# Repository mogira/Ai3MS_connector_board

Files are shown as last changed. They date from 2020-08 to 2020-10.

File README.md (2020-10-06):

# Anycubic i3 Mega S Connector Board
## Overview
This is the project to create the connector board for ["MONOBLOCK" ANYUCBIC I3 MEGA-S Direct Extruder MOD add BLTouch by Toshi_Yamamoto](https://www.thingiverse.com/thing:4035830).  
The board accepts BLTouch, Extruder Motor and the extension cords to these from motherboard additinally.

### Remarks
**If you need switch, capacitors and resistors of the stock board, you can not use this board because I removed them.**

<br />

## [>> Build Guide](docs/build_guide.md)

<br />

## [>> CADLAB.io](https://cadlab.io/node/23246/)

<br />

## [>> Circuit Board Gallery](docs/circuit_board_gallery.md)

<br />

## Gallery
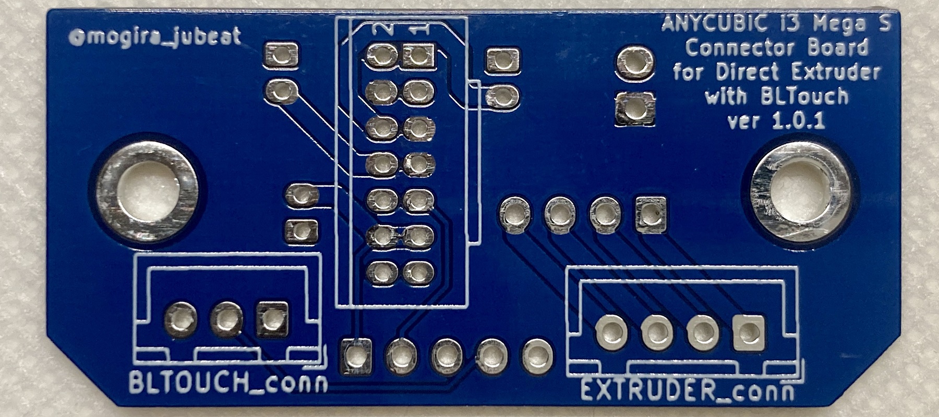
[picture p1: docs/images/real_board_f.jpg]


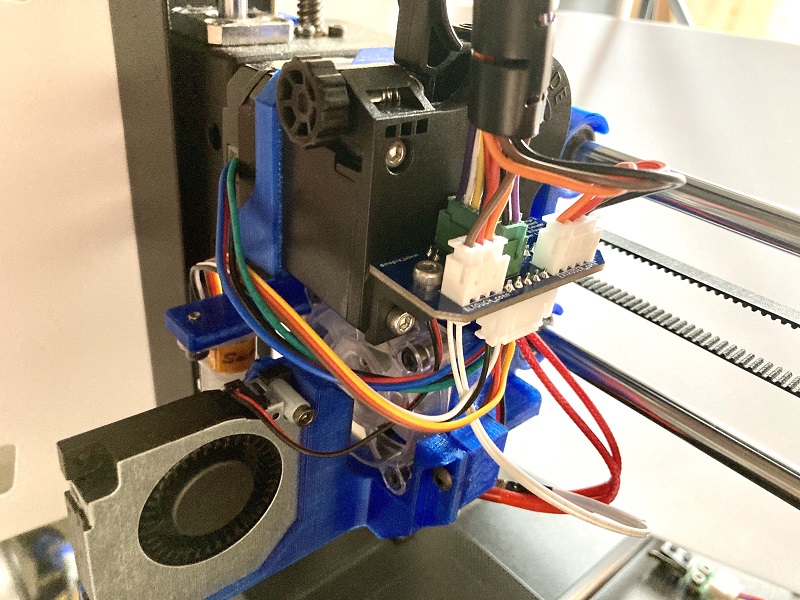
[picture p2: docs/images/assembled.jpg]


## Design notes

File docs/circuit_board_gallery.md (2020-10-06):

# Cuircuit Board Gallery

| | Front | Back |
|-|---|---|
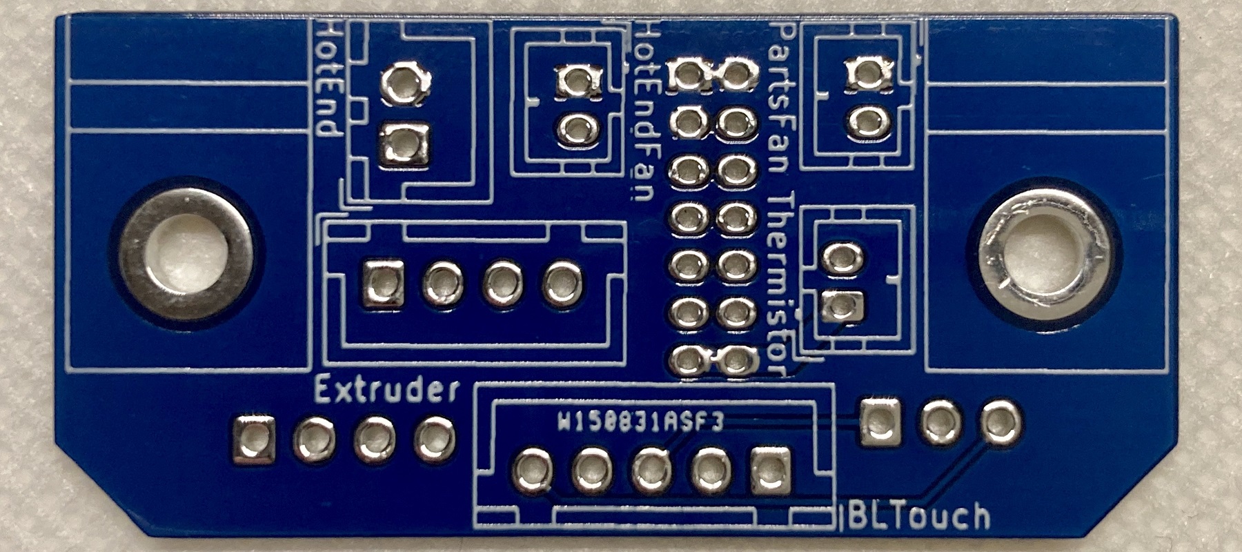
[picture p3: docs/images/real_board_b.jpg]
| Real Board |  |  |
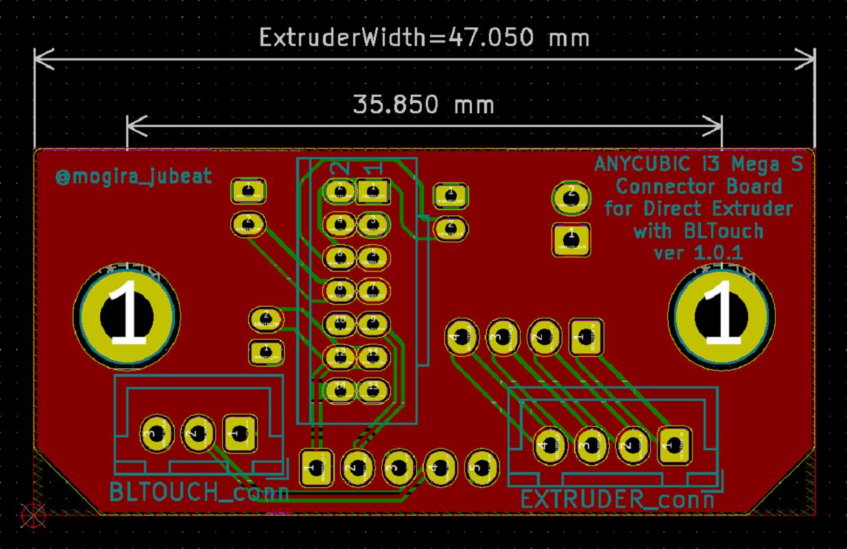
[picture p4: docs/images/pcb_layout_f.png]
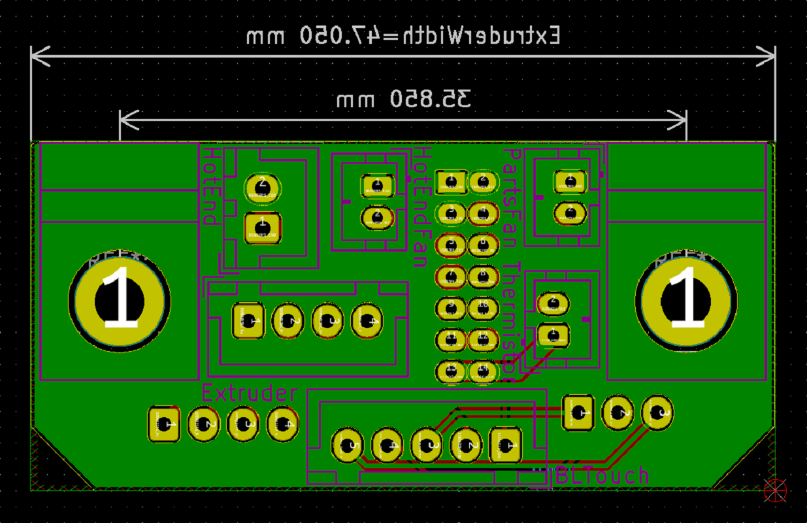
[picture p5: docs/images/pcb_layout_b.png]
| Layout |  |  |

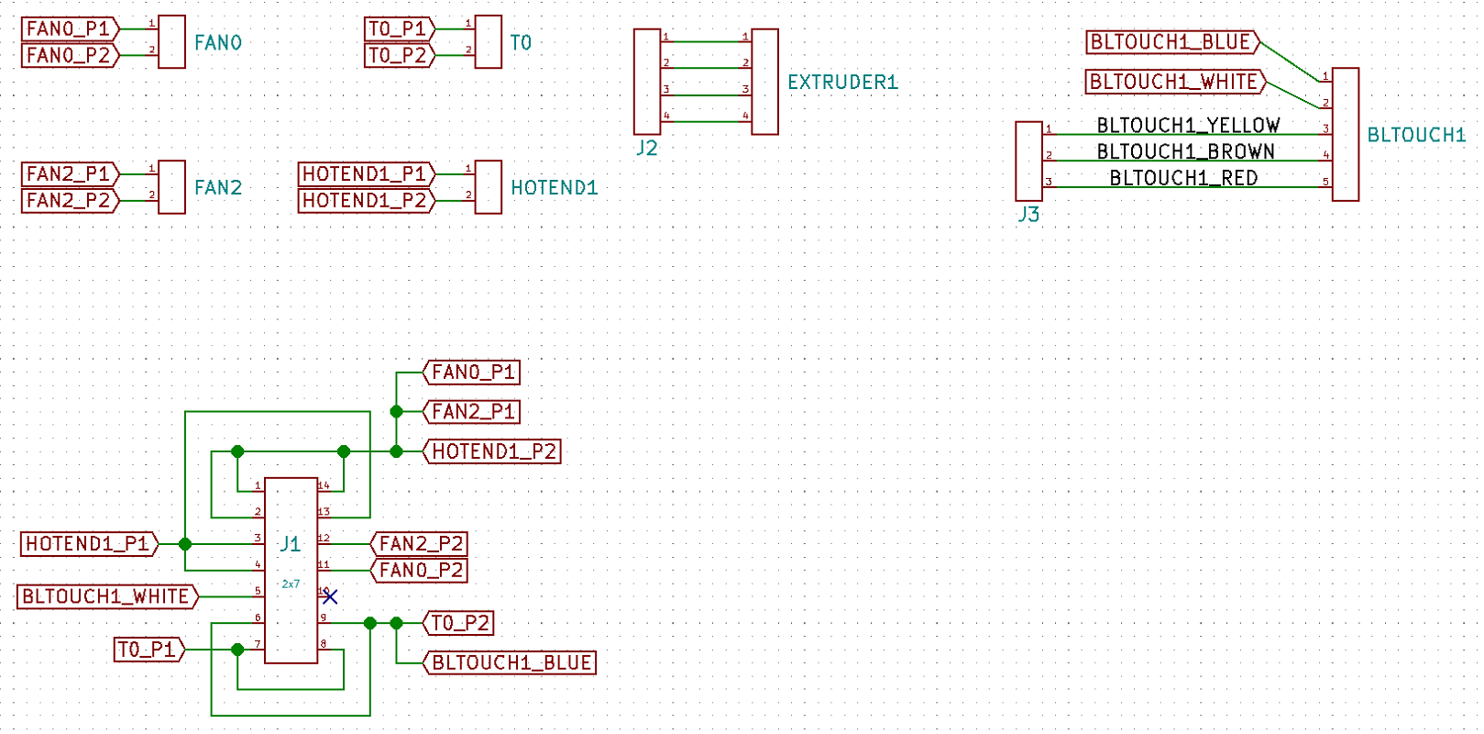
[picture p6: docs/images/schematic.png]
| Schematic |  |
|-|-|

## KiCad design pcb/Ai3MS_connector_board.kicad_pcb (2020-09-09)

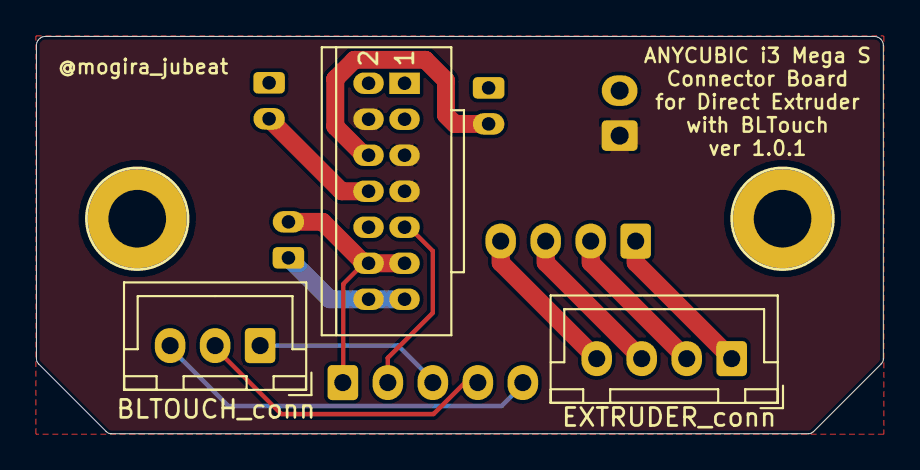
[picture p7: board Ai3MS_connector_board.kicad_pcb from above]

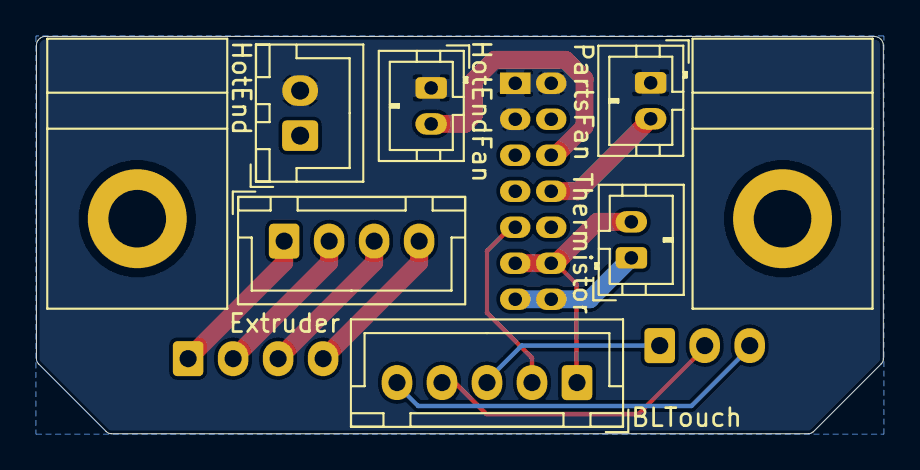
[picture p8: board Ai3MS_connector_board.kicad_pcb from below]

Board: 2 copper layers, 47.0 x 22.1 mm, 9 parts (6 on the bottom side), 14 nets.

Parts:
BLTOUCH_conn: 1x3_rev; JST_XH_B3B-XH-A_1x03_P2.50mm_Vertical
BLTouch: 1x5; JST_XH_B5B-XH-A_1x05_P2.50mm_Vertical
EXTRUDER_conn: 1x4_rev; JST_XH_B4B-XH-A_1x04_P2.50mm_Vertical
Extruder: 1x4; JST_XH_B4B-XH-A_1x04_P2.50mm_Vertical
HotEnd: 1x2; JST_XH_B2B-XH-A_1x02_P2.50mm_Vertical
HotEndFan: 1x2; JST_PH_B2B-PH-K_1x02_P2.00mm_Vertical
J1: 2x7; 2x7_2mm-pitch_Lock_GreenConnector
PartsFan: 1x2; JST_PH_B2B-PH-K_1x02_P2.00mm_Vertical
Thermistor: 1x2; JST_PH_B2B-PH-K_1x02_P2.00mm_Vertical

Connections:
/BLTOUCH1_SERVO_5V: BLTOUCH_conn.3, BLTouch.5
/BLTOUCH1_SERVO_CONTROL: BLTOUCH_conn.1, BLTouch.3
/BLTOUCH1_SERVO_GND: BLTOUCH_conn.2, BLTouch.4
/EXTRUDER1_A+: EXTRUDER_conn.1, Extruder.1
/EXTRUDER1_A-: EXTRUDER_conn.2, Extruder.2
/EXTRUDER1_B+: EXTRUDER_conn.3, Extruder.3
/EXTRUDER1_B-: EXTRUDER_conn.4, Extruder.4
BLTOUCH1_GND: BLTouch.1, J1.11, J1.12, Thermistor.2
BLTOUCH1_ZMIN: BLTouch.2, J1.9
HEATER1_12V: HotEnd.2, HotEndFan.1, J1.1, J1.2, J1.3, PartsFan.1
HEATER1_GND: HotEnd.1, J1.4, J1.5, J1.7
HOTENDFAN1_GND: HotEndFan.2, J1.6
PARTFAN1_GND: J1.8, PartsFan.2
THERMISTOR1_DATA: J1.13, J1.14, Thermistor.1

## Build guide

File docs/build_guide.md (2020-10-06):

# Build Guide
## Parts List
| Name | Quantity | Remark |
|---|:---:|---|
| MAC8 AXA-15-M3-3.2 | 2 | (can use but not recommend) or AXA-15-M3 |
| (2x7 2mm Pitch) Green Connector | 1 | transplant from the stock board |
| JST **PH** Female Connector 1x2 | 3 | |
| JST XH Female Connector 1x2 | 1 | |
| JST XH Female Connector 1x2 | 1 | |
| JST XH Female Connector 1x3 | 1 | |
| JST XH Female Connector 1x4 | 2 | |
| JST XH Female Connector 1x5 | 1 | |
| JST XH Male Connector 1x3 | 1 | |
| JST XH Male Connector 1x4 | 2 | |
| JST XH Male Connector 1x5 | 1 | |
| JST XH Connector Contact | 16 | |
| Dupont/QI/2550 Connector 1x1 | 3 | |
| Dupont/QI/2550 Connector Contact| 3 | |
| M3 Screw 50mm | 1 | |
| M3 Screw 30mm | 1 | |
| M3 Screw 6mm | 2 | |

And you need a crimp tool. I recommend "ENGINEER PA-09" to crimp XH and PH connectors.

<br />

## Notes
* Silks are changed from the stock board as below:
    * T0 -> Thermistor
    * FAN0 -> PartsFan
    * FAN2 -> HotEndFan

<br />

## Procedures
### 1. Remove the parts from the stock board
You must remove the Green Connector to transplant to the new board.  
About the other connectors, do as you like.  
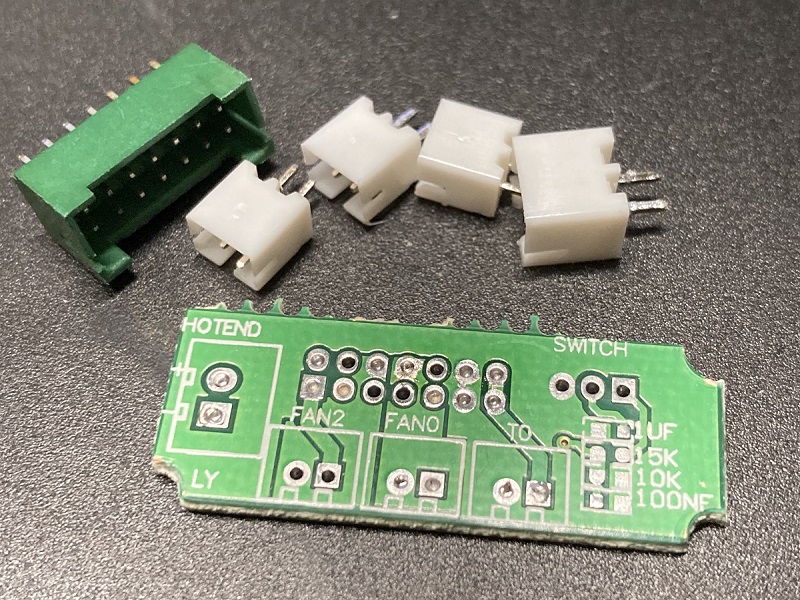
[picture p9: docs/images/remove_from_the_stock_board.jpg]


<br />

### 2. Expand the holes with drill
#### **AXA-15-M3 (recommend)**
If you substitute AXA-15-M3 for AXA-15-M3-3.2, it is better to expand the screw hole on the extruder side of it to 3.2mm (M3 Clearance hole size).  
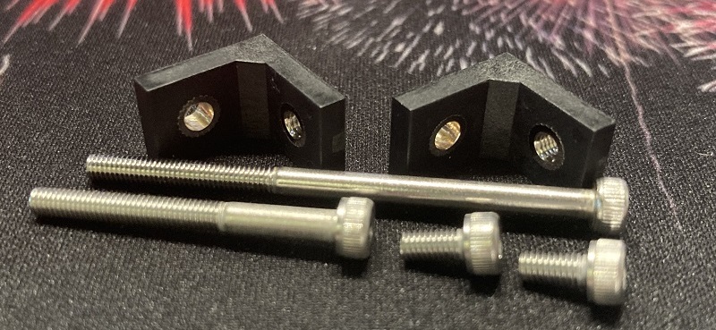
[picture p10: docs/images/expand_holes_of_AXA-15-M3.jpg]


<br />

### 3. Solder the parts to the board
It is easier to implement the GreenConnector firstly.  
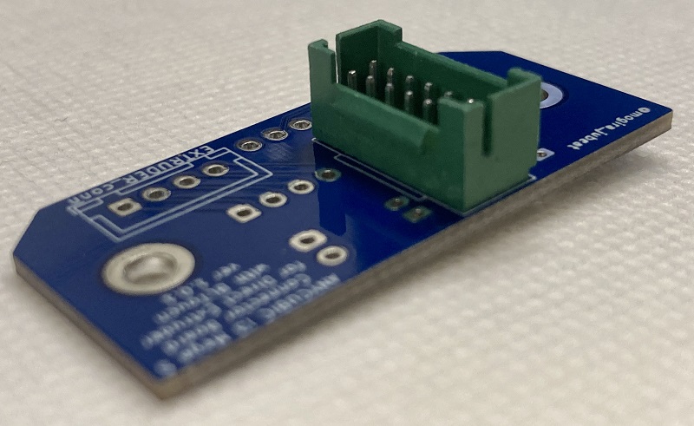
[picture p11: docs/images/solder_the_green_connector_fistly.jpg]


<br />

### 4. Crimp the connectors
You should crimp the following connectors:
* BLTOUCH_conn (1x3 XH)  
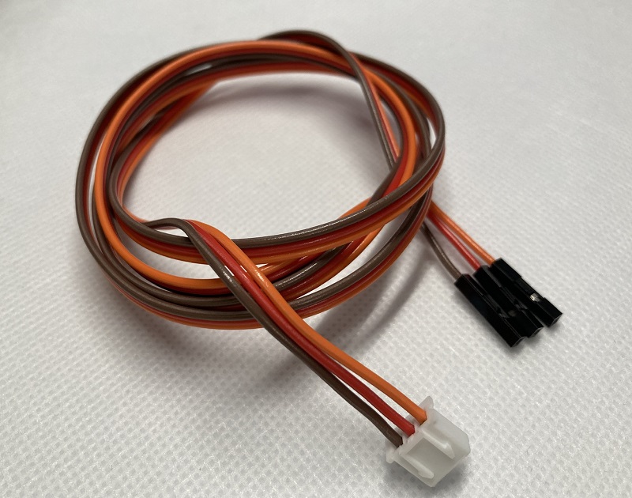
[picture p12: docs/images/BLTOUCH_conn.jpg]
  
* EXTRUDER_conn (1x4 XH)  
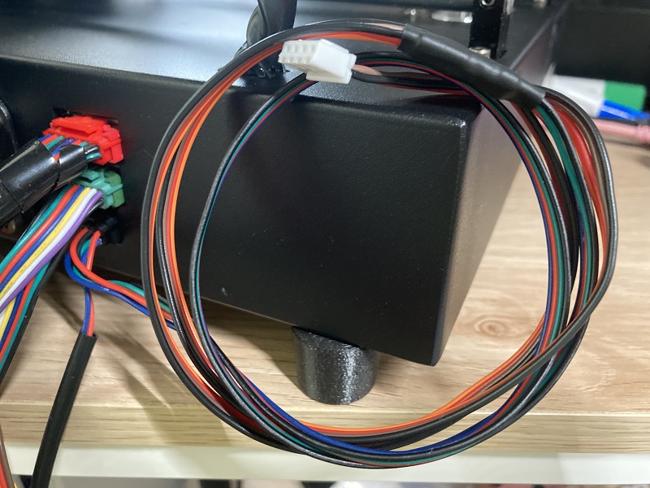
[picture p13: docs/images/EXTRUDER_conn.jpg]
    
  \* You should extend the Extruder connector cable to the print head.
* BLTouch (1x5 XH)  
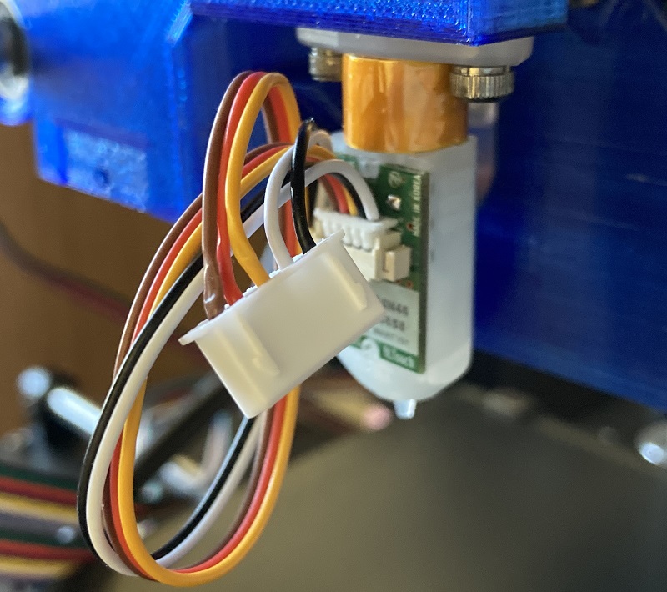
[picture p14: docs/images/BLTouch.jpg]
  
* Extruder (1x4 XH)  
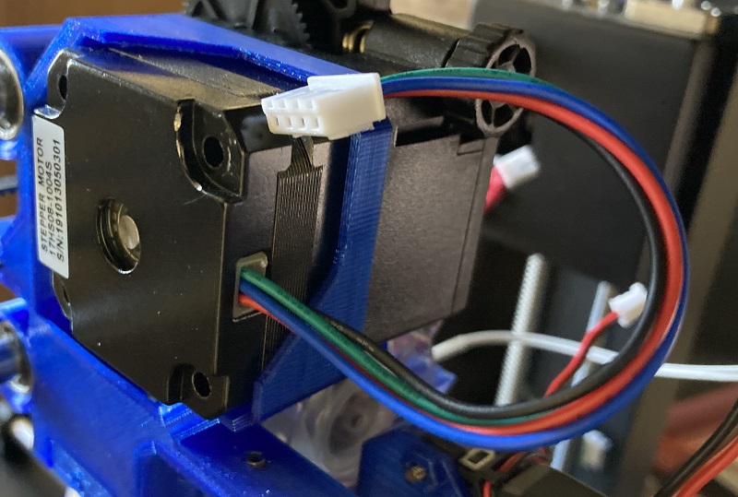
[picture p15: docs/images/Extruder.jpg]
  

<br />

### 5. Assemble
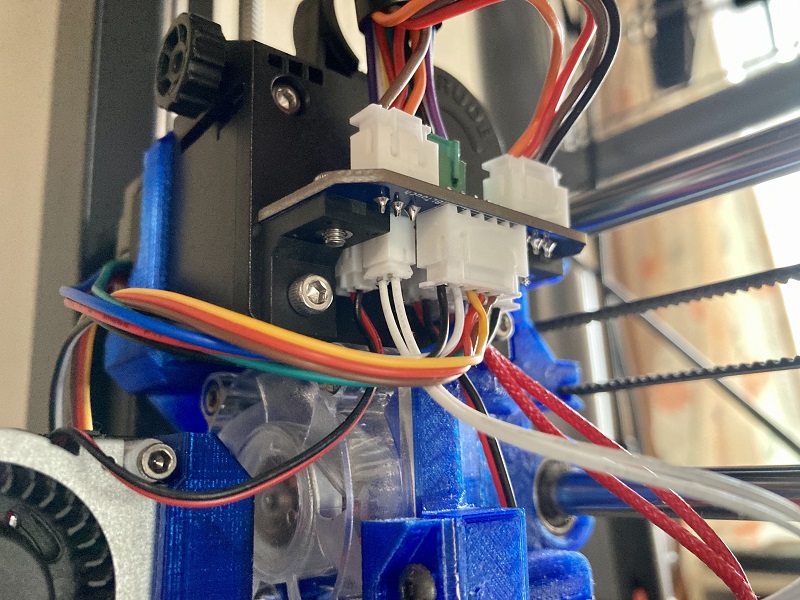
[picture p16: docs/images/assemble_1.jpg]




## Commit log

2020-08-11 Reproduce the electrical connection of the stock board
    [Ai3MS_connector_board.kicad_pcb, Ai3MS_connector_board.sch]
2020-08-11 Add EXTRUDER and BLTOUCH
    [Ai3MS_connector_board.sch]
2020-08-11 Remove SWITCH, Capacitors and Resistors
    [Ai3MS_connector_board.sch]
2020-08-22 Move kicad files to "pcb" directory
    [Ai3MS_connector_board.kicad_pcb, Ai3MS_connector_board.sch]
2020-09-01 Export symbols and footprints to libraries
    [Ai3MS_connector_board.kicad_pcb, Ai3MS_connector_board.sch]
2020-09-08 Improve AXA-15-M3
    * Fix hole size
    * Add backside silk for the screw head
    * Add 0.5mm local clearance for the pad
    * Add 3d model
    [Ai3MS_connector_board.kicad_pcb]
2020-09-08 Improve links
    * Change link names
    * Change connection paths
    * Retouch PCB due to loading new net file
    * Note: HEATER's 12V/GND is inversed of others. Pin#1 is GND, Pin#2 is 12V.
    [Ai3MS_connector_board.kicad_pcb, Ai3MS_connector_board.sch]
2020-09-08 Round four corners
    [Ai3MS_connector_board.kicad_pcb]
2020-09-08 Improve 2x7_2mm-pitch_Lock_GreenConnector
    * Renamed from "PHLike_Green_Connector"
    * Fix pin assign of symbol "2x7"
    * Fix pin assign of footprint "2x7_2mm-pitch_Lock_GreenConnector"
    * Update silk
    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
    [Ai3MS_connector_board.kicad_pcb, Ai3MS_connector_board.sch]
2020-09-09 Fix upper right silk
    * From "ANYCUBIC i3 Mega" to "ANYCUBIC i3 Mega S"
    * Update version string
    [Ai3MS_connector_board.kicad_pcb]
2020-09-09 Generate drill and gerber files
    [Ai3MS_connector_board-B_Cu.gbl, Ai3MS_connector_board-B_Mask.gbs, Ai3MS_connector_board-B_SilkS.gbo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]
